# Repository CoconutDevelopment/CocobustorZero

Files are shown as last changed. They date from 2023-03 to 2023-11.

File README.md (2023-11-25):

# CocobustorZero
Voron0

An small upgrade for the Voron 0.2 to make it print slightly faster
BASED ON VORONDESIGN V0.1 https://github.com/VoronDesign/Voron-0
Inspired by 247/0 Beta2

(FORMBOT Full kit possibly comming your way soon)
Join my discord if you want : https://discord.gg/AjryAUX7Z3

Design goals:
- Speedbenchy WR (Sub 2-minute)
  - 1000mm/s Velocity
  - 300000mm/s^2 Acceleration

- 4 motor NEMA17 4WD
  - 48-60mm NEMA17 support
  - Separate control board

- Triple Belted z (worm gearing)
  - Fast Z hops and no z binding
  - Auto bed tramming
  - Ultralow Profile

- External cooling
  - Coconut's Triple Fan Ducts
  - 12KPA CPAP fan

- Extremely Lightweight X gantry
  - Cnc X carriage
  - Bowden Ultralight Toolhead
  - External esp
  - Ultralight Xy joints
  - CNC hollowed mgn7 rail

- Nema17 4WD Coconut edition
  - Extreme motor grip (200+ degrees)
  - Straight belt path
  - Integrated motor idlers
  - Fits all in the back

- Enclosure
    - Has to be enclosable using the 0.2 Tophat
    - Has to be ABS capable
    - All part cooling must draw enclosure air

- M4 Max
    - Strongest extruder possible
    - Double Shear
    - Short Bowden tube

Upgrades:
- 247/0 Beta2 (By 247printing https://247printing.gumroad.com/) (Inspiration)
- AWD NEMA17 V0 CE (V2 Is reccomended) (By Coconut)
- AWD NEMA17 V0 LE (By LittleTimTim https://github.com/LittleTimTim/V0-AWD-Tim-Style)
- Dual Lrs-150s (By Coconut)
- Vzbot inspired frame braces (By Kl3pt https://www.printables.com/model/450049-voron-v0-frame-brace)
- Skr mini e3 v2 + Annex Constellation supernova
- 48V Meanwell UHP-500-48
- Ultralightweight X gantry + XY joints
- Modded Thick Belted Z (By MathmaticalPotato https://github.com/VoronDesign/VoronUsers/tree/master/printer_mods/MathematicalPotato/v0.1_belted_z_drive)
- Coconut triple fan ducts (By Coconut)

Coconut's V0 AWD V2 mod
(On RC1)

https://github.com/CoconutDevelopment/CocobustorZero/assets/110824572/ccff1a14-459e-45de-a45c-08869c3bc4b1

LittleTimTim's V0 AWD mod https://github.com/LittleTimTim/V0-AWD-Tim-Style

https://github.com/CoconutDevelopment/Stock-Voron-0/assets/110824572/6bcad486-bbd0-41eb-bcec-efc06d3bc0a4

Gallery:
Voron0Back

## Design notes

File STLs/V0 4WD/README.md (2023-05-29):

How to choose a awd

Awd TE (Tim edition) and Awd CE (Coconut edition) are very similar in their design, they both have top and bottom motor plates and tensioners.
The difference between them is coconut awd keeps the belt path straight and uses the motors themselves to tension (using an m5 screw) but it uses 4 more idlers (8 more bearings) than tim edition, and is optimized for maximum grip on the motor pulley. While Tim edition uses the middle idler to tension the belts and may not have as much grip.

Please make an imformed descision and this is biased as it is written by coconut, timtim has allowed me to use his files on this repo but you can also visit his own.
Also note that the text above is in referenace to AWD v2 CE, awd v1 does not have tensioners and is no longer maintained.

If you have questions please ask me on the voron discord in the v0 user mods channel (Coconut #1567) Thank you!

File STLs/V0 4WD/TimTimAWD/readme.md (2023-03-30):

# V0-AWD-Tim-Style
Quad motor v0 XY with tensioner

This design was inspired by Coconut & FailFast

Materials needed:

-random filament (I used CF PETG, ABS will do fine) 

-1 printed Top

-1 printed Bottom

-2 printed Uspacers

-28 F623ZZ Flanged Ball Bearing 3x10x4mm (If you print the stock 9mm spacers you don't need as many)

-28 3x5x0.5 mm Shim Spacer Washers

-23 M3x35 Bolts

-8 M3x8-10-12 (I don't remember what exactly I used but one of those)

-4 GT2 20t pulleys 5mm bore

-4 nema 17 steppers of your choice

-4 heatset inserts

-stock y endstop switch & screws

-5 mm GT2 belt width 6mm

-control board that supports at least 6 stepper drivers (I'm using a btt octopus)

Assembly:

Just put it together, if you're building this I trust you.

Tensioning:

When initially installing belts you can leave the slotted center idler loose, 
once belt is installed you can push idler from the build volume side until tensioned
as desired and tighen.

Klipper config:

you'll need to add a stepper_x1 and stepper_y1 with proper pinout and coresponding driver section,
I'll provide my current config in this folder





https://user-images.githubusercontent.com/129321661/228639436-86d11ff1-20ca-46b5-aa57-27f5ffe6771b.mp4

https://user-images.githubusercontent.com/129321661/228639209-f505d235-a20b-4d33-a5d6-68dab8504cda.mp4

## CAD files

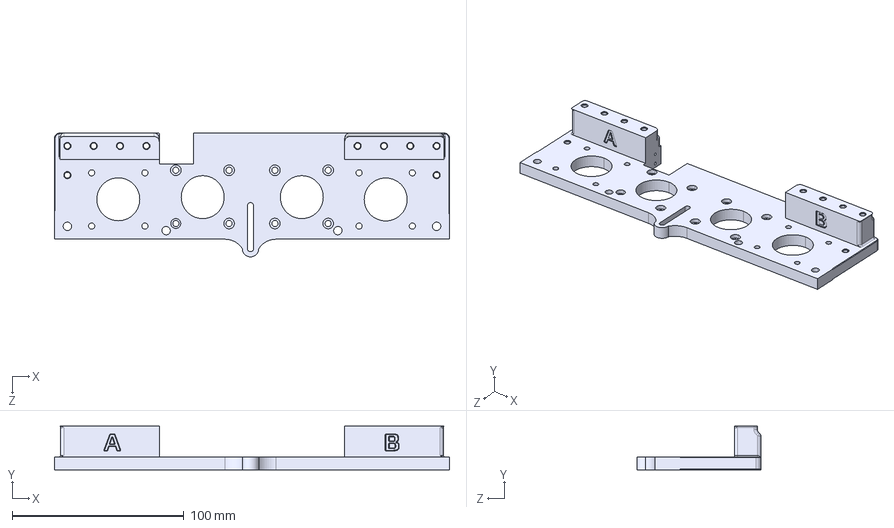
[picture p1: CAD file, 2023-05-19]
STLs/V0 4WD/TimTimAWD/STEP/bottomTotalAssembly.STEP
230.0 x 25.5 x 72.1 mm

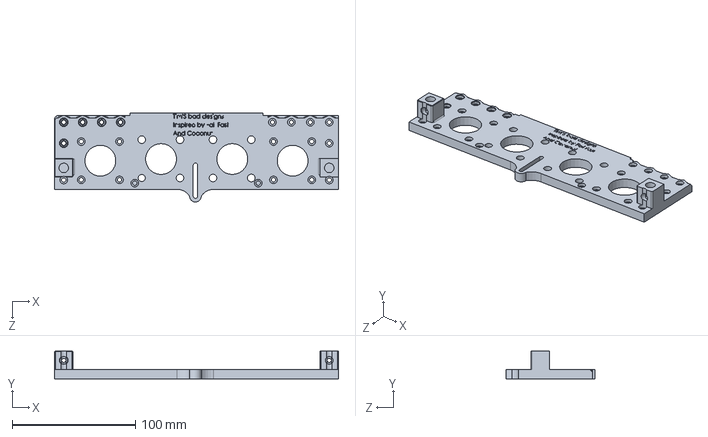
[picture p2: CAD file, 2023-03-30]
STLs/V0 4WD/TimTimAWD/SLDPRTs/TopTotalAssembly.SLDPRT
230.0 x 22.5 x 72.1 mm

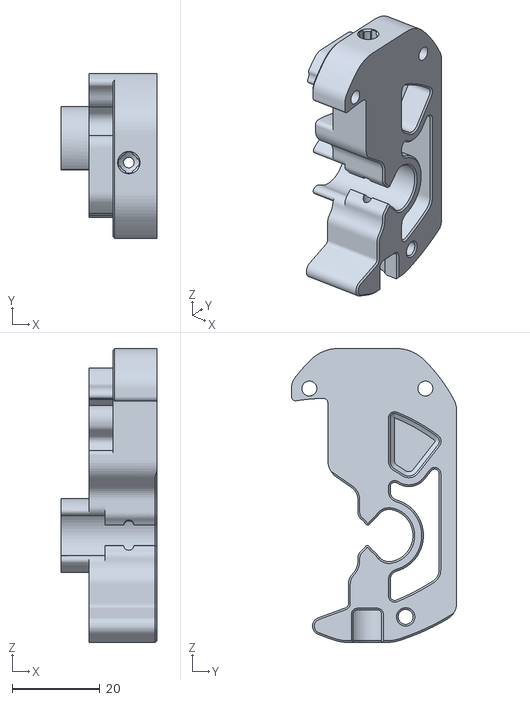
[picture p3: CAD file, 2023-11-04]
STLs/M4max/Main_Body_x1.stl
21.8 x 37.6 x 66.8

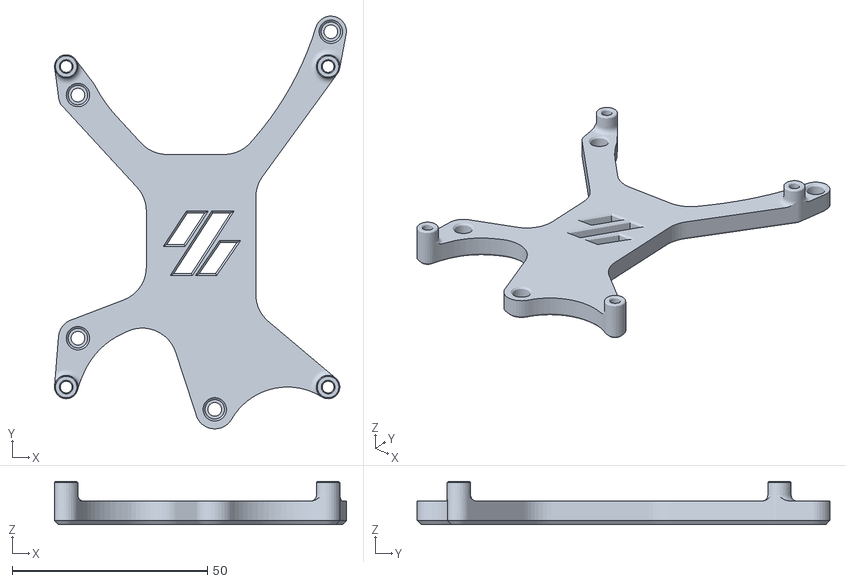
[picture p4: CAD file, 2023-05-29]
STLs/AnnexSupernova/Annex_Supernova_Bracket_Skr_Holes_x1.stl
74.7 x 105.6 x 11.0

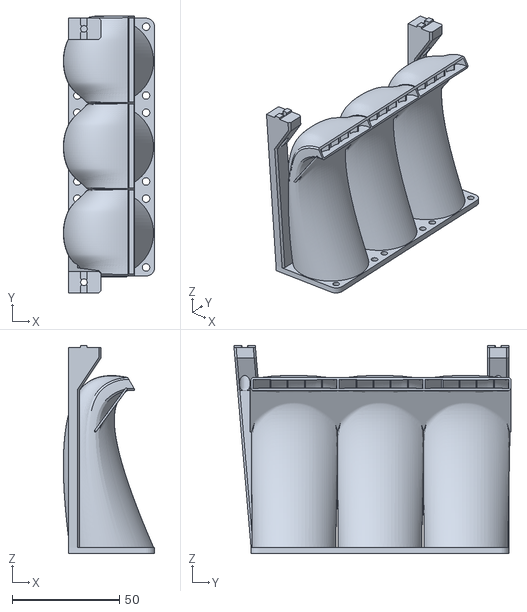
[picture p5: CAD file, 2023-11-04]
STLs/Coconut Air Ducts/[a]_Left_Duct_x1.stl
42.5 x 128.9 x 97.0

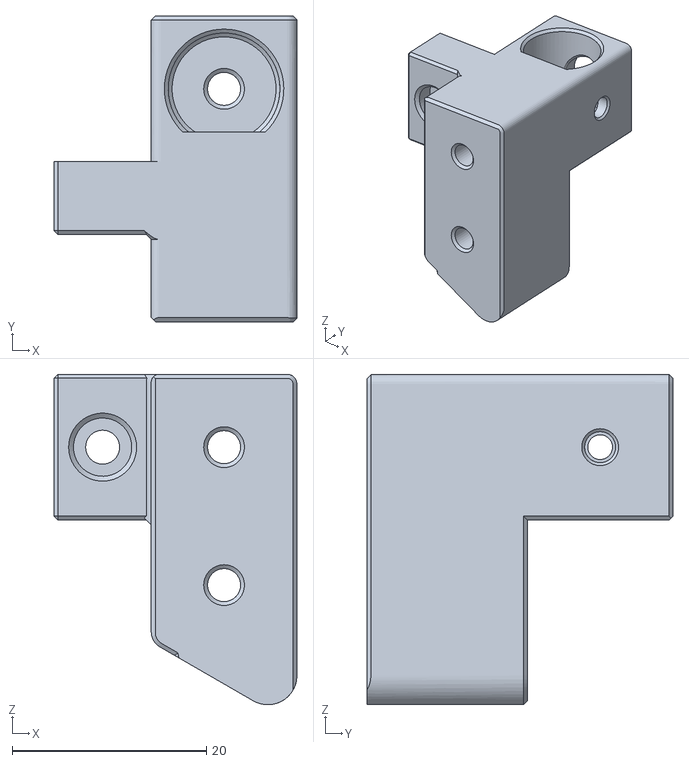
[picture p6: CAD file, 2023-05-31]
STLs/FrontXBeam/A_Upper_Idler_x1.stl
25.0 x 31.5 x 34.0

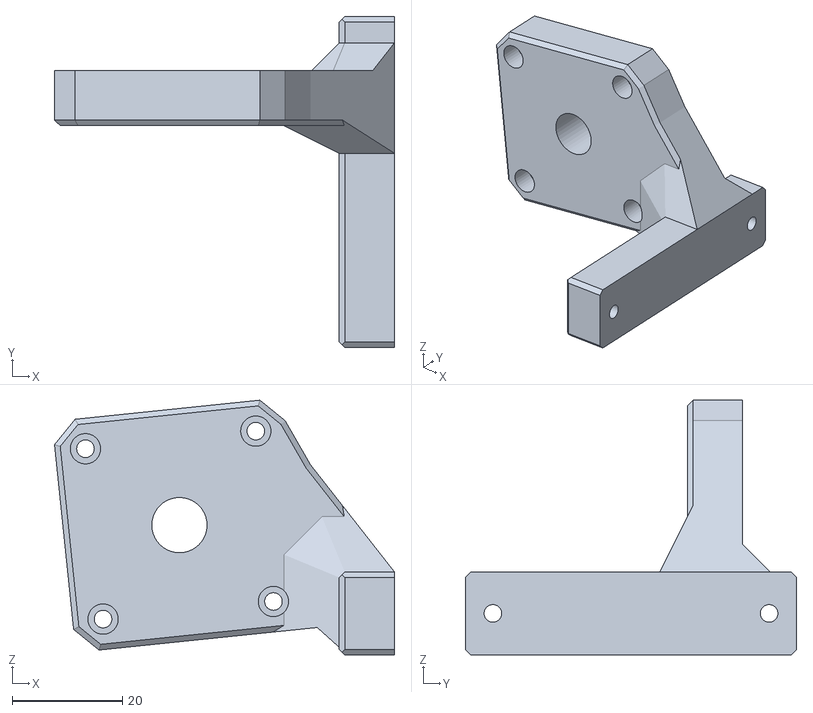
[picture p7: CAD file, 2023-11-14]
STLs/M4max/M4_Max_Motor_Support_x1.stl
61.5 x 60.0 x 46.1

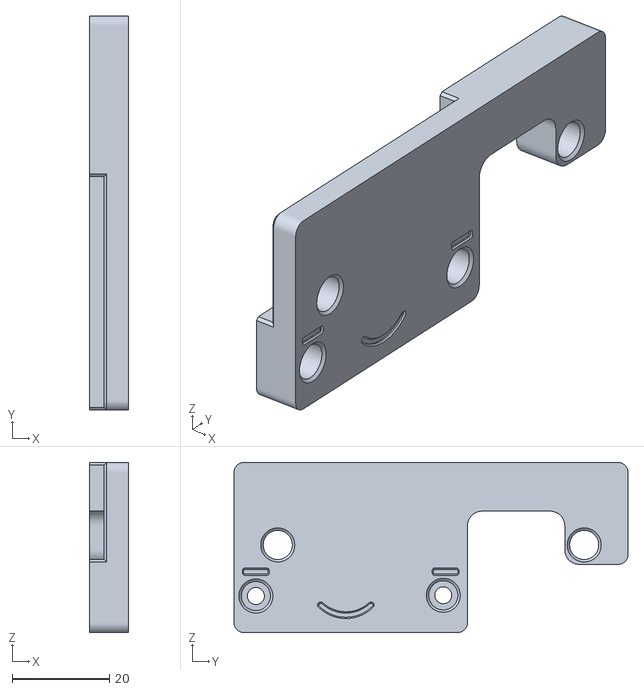
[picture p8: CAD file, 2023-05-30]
STLs/Meanwell UHP-500/[a]_Meanwell_UHP-500_Mount_Lower_x1.stl
8.00 x 81.0 x 35.0

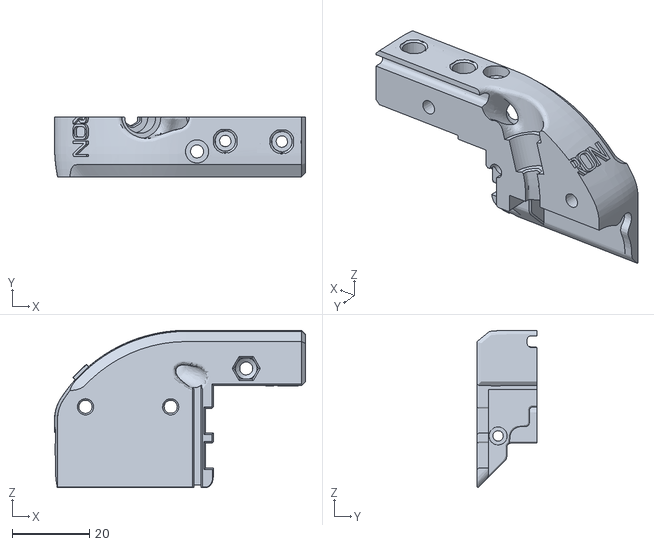
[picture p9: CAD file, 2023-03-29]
STLs/MGN9C X Mosq (Not reccomended)/MGN9CRight.stl
64.8 x 15.4 x 40.6

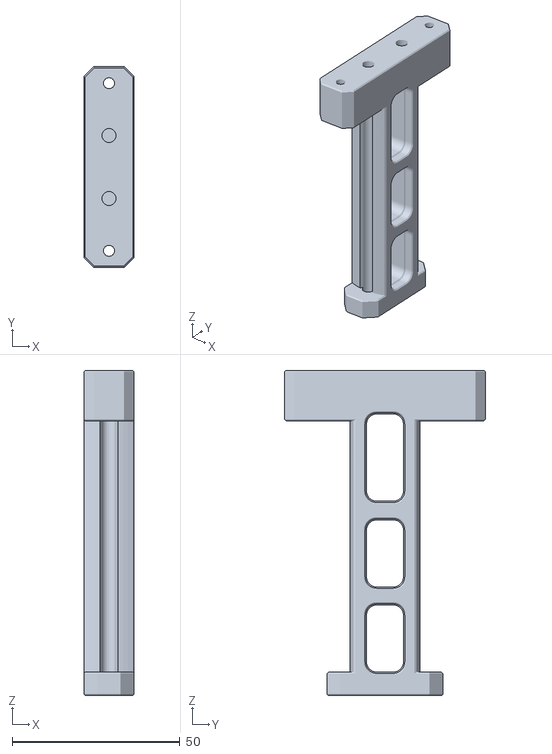
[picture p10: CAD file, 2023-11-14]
STLs/PanelAttachments/Extended_Spool_Holder_x1.stl
15.0 x 60.0 x 97.0

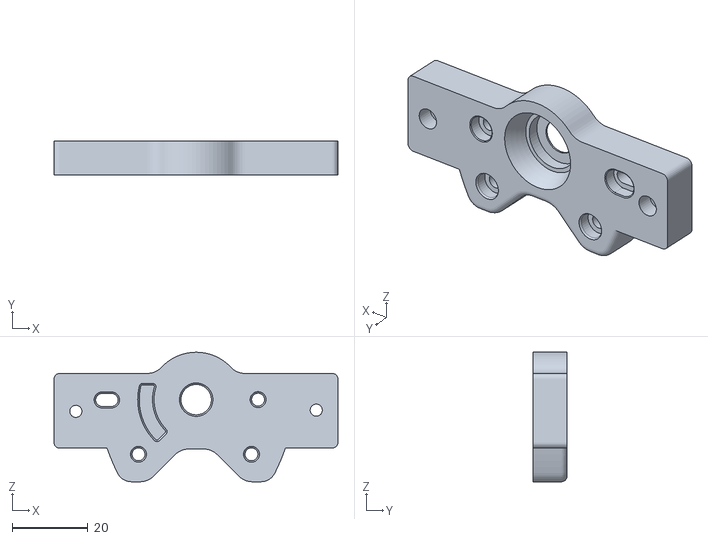
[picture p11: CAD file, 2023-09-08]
STLs/Thick Belted z/Belted_Z_Midplate_x1.stl
74.8 x 9.00 x 34.1

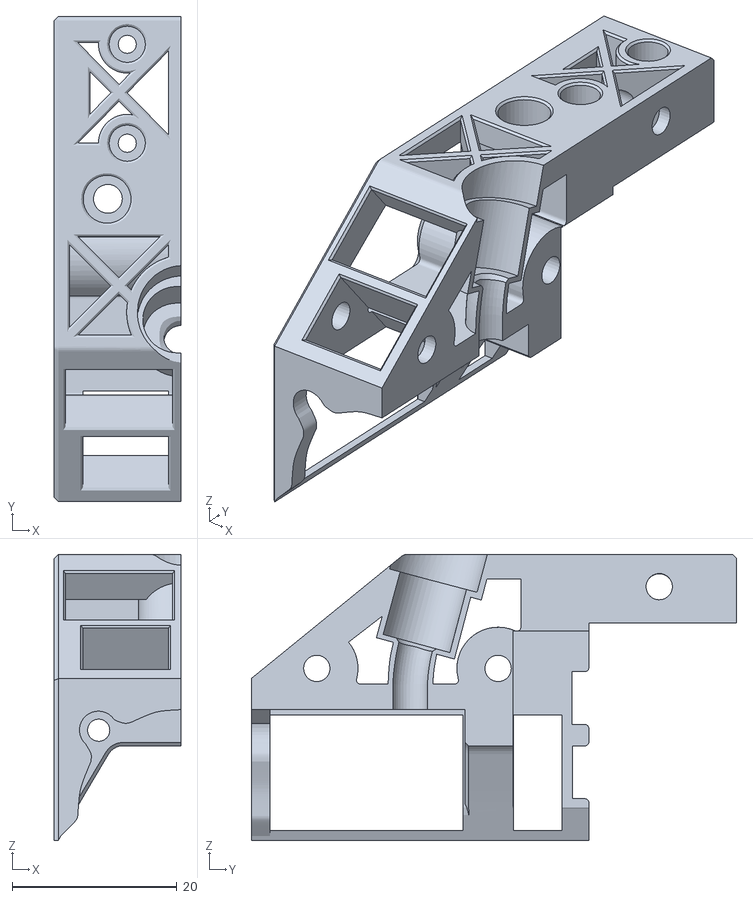
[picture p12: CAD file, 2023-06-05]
STLs/ULW X Gantry/Toolhead/Ultralightweight_Carriage_Left_x1.stl
15.4 x 58.9 x 34.7

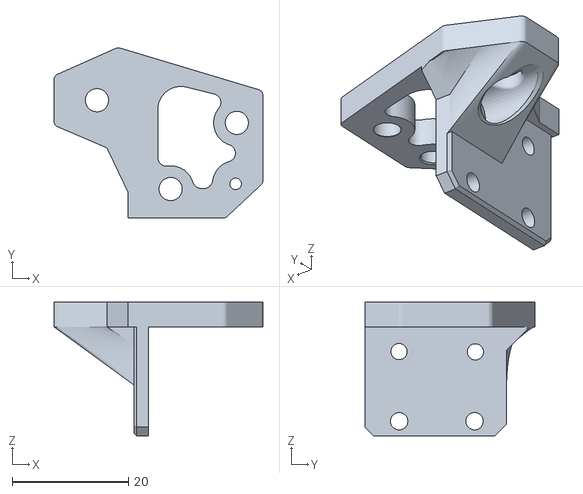
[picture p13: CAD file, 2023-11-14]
STLs/ULW X Gantry/XY Joints/XY_Joint_Right_Lower_x1.stl
36.0 x 29.4 x 23.0

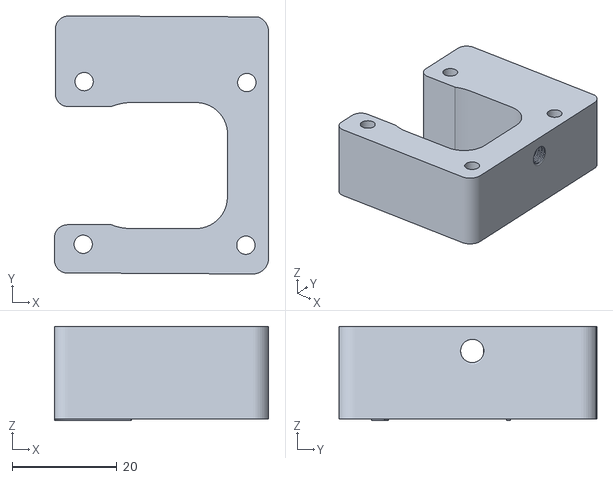
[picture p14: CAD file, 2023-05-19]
STLs/V0 4WD/CoconutAWD/v2AWD (Latest)/[a]_AMotorSpacer_x1.stl
40.8 x 49.2 x 18.0

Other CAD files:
STLs/V0 4WD/TimTimAWD/SLDPRTs/CompleteAWD.SLDASM
STLs/FrontXBeam/B_Upper_Idler_x1.stl
STLs/M4max/End_Plate_x1.stl
STLs/Meanwell UHP-500/[a]_Meanwell_UHP-500_Mount_Upper_x1.stl
STLs/Archived/MGN9C X Mosq/MGN9CLeft_x1.stl
STLs/Archived/V1AWD (OLD)/ABDriveMotorPlate.stl
STLs/Archived/V1AWD (OLD)/ADriveCap.stl
STLs/Archived/V1AWD (OLD)/BDriveCap.stl
STLs/Archived/V1AWD (OLD)/MotorSpacerA.stl
STLs/Archived/V1AWD (OLD)/MotorSpacerB.stl
STLs/M4max/Bottom_Plate_x1.stl
STLs/M4max/Middle_Plate_x1.stl
STLs/M4max/[a]_Guider_x1.stl
STLs/M4max/[a]_Latch_Shuttle.stl
STLs/M4max/[a]_Latch_x1.stl
STLs/MGN9C X Mosq (Not reccomended)/MGN9CLeft.stl
STLs/Superwide Stance/Unfinished (2).stl
STLs/Superwide Stance/Unfinished (3).stl
STLs/Superwide Stance/Unfinished (4).stl
STLs/Superwide Stance/Unfinished.stl
STLs/Thick Belted z/Belted_Z_Back_Plate_x1.stl
STLs/Thick Belted z/Belted_Z_Baseplate_x1.stl
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

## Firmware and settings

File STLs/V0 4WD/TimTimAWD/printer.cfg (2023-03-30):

[include fluidd.cfg]
# This file contains common pin mappings for the BIGTREETECH SKR mini
# E3 v3.0. To use this config, the firmware should be compiled for the
# STM32G0B1 with a "8KiB bootloader" and USB communication.

# The "make flash" command does not work on the SKR mini E3. Instead,
# after running "make", copy the generated "out/klipper.bin" file to a
# file named "firmware.bin" on an SD card and then restart the SKR
# mini E3 with that SD card.

## Voron Design VORON 0.2 SKR Mini E3 V3 config

## *** THINGS TO CHANGE/CHECK: ***
## MCU path                                                                     [mcu] section
## Z and Extruder motor currents                                                [tmc2209 stepper_*] sections. Uncomment the stepper motor you have
## Full steps per rotation for Extruder                                         [extruder] section
## Thermistor types                                                             [extruder] and [heater_bed] sections - See https://www.klipper3d.org/Config_Reference.html#common-thermistors for common thermistor types
## Extruder motor currents                                                      [extruder] section
## PID tune                                                                     [extruder] and [heater_bed] sections
## Fine tune E steps                                                            [extruder] section
## For more info                                                                check https://docs.vorondesign.com/build/startup/#v0

[mcu]
#####################################################################
# Obtain definition by "ls -l /dev/serial/by-id/"
#####################################################################
serial:/dev/serial/by-id/usb-Klipper_stm32f446xx_280022001750344D30353320-if00

[temperature_sensor mcu_temp]
sensor_type: temperature_mcu
min_temp: 0
max_temp: 100

[temperature_sensor host_temp]
sensor_type: temperature_host
min_temp: 10
max_temp: 100

[printer]
kinematics: corexy
max_velocity: 1200
max_accel: 50000
max_z_velocity: 300
max_z_accel: 200
square_corner_velocity: 50

#####################################################################
#   Fan Control
#####################################################################

[heater_fan hotend_fan]
# FAN1
pin: PD13
max_power: 1.0
kick_start_time: 0.5
heater: extruder
heater_temp: 50.0
#fan_speed: 1.0                                                     # You can't PWM the delta fan unless using blue wire

[fan]
# FAN0
pin: PD12
max_power: 1.0
kick_start_time: 0.5                                                # Depending on your fan, you may need to increase this value if your fan will not start
off_below: 0.13
cycle_time: 0.010


#####################################################################
#   Homing and Gantry Adjustment Routines
#####################################################################


[safe_z_home]
home_xy_position: 60,60 										# these coordinates must NOT be greater than the values specified in "position_max:" for the X and Y steppers
speed: 50.0
z_hop: 5

## To be used with BED_SCREWS_ADJUST
[bed_screws]
screw1: 60,5
screw1_name: front screw
screw2: 5,115
screw2_name: back left
screw3: 115,115
screw3_name: back right


#####################################################################
#   V0 Display
#####################################################################
# [mcu display]
# serial: **PASTE YOUR SERIAL PORT HERE AND UNCOMMENT**
# restart_method: command

# [display]
# lcd_type: sh1106
# i2c_mcu: display
# i2c_bus: i2c1a
# # Set the direction of the encoder wheel
# #   Standard: Right (clockwise) scrolls down or increases values. Left (counter-clockwise scrolls up or decreases values.
# encoder_pins: ^display:PA3, ^display:PA4
# #   Reversed: Right (clockwise) scrolls up or decreases values. Left (counter-clockwise scrolls down or increases values.
# #encoder_pins: ^display:PA4, ^display:PA3
# click_pin: ^!display:PA1
# kill_pin: ^!display:PA5
# #x_offset: 2
# #   Use X offset to shift the display towards the right. Value can be 0 to 3
# #vcomh: 0
# #   Set the Vcomh value on SSD1306/SH1106 displays. This value is
# #   associated with a "smearing" effect on some OLED displays. The
# #   value may range from 0 to 63. Default is 0.
# #   Adjust this value if you get some vertical stripes on your display. (31 seems to be a good value)

# [neopixel displayStatus]
# pin: display:PA0
# chain_count: 1
# color_order: GRB
# initial_RED: 0.2
# initial_GREEN: 0.05
# initial_BLUE: 0

# This file contains common pin mappings for the BigTreeTech Octopus
# and Octopus Pro boards. To use this config, start by identifying the
# micro-controller on the board - it may be an STM32F446, STM32F429,
# or an STM32H723.  Select the appropriate micro-controller in "make
# menuconfig" and select "Enable low-level configuration options". For
# STM32F446 boards the firmware should be compiled with a "32KiB
# bootloader" and a "12MHz crystal" clock reference. For STM32F429
# boards use a "32KiB bootloader" and an "8MHz crystal". For STM32H723
# boards use a "128KiB bootloader" and a "25Mhz crystal".

# See docs/Config_Reference.md for a description of parameters.

# Driver0
[stepper_x]
step_pin: PF13
dir_pin: PF12
enable_pin: !PF14
microsteps: 16
rotation_distance: 40
endstop_pin: PG11
position_endstop: 10
position_max: 110
homing_speed: 50

# Driver1
[stepper_y]
step_pin: PG0
dir_pin: PG1
enable_pin: !PF15
microsteps: 16
rotation_distance: 40
endstop_pin: PG10
position_endstop: 0
position_max: 120
homing_speed: 50

# Driver2
#[stepper_z]
#step_pin: PF11
#dir_pin: PG3
#enable_pin: !PG5
#microsteps: 16
#rotation_distance: 8
#endstop_pin: PG10
#position_endstop: 0.5
#position_max: 200

# Driver3
# The Octopus only has 4 heater outputs which leaves an extra stepper
# This can be used for a second Z stepper, dual_carriage, extruder co-stepper,
# or other accesory such as an MMU
#[stepper_]
#step_pin: PG4
#dir_pin: PC1
#enable_pin: PA0
#endstop_pin: PG11
#...

#Driver4
[stepper_x1]
step_pin: PF9
dir_pin: PF10
enable_pin: !PG2
microsteps: 16
rotation_distance: 40
#endstop_pin:  PG11 # T0
#position_endstop: 10
#position_max: 110
#homing_speed: 50

#[filament_switch_sensor material_0]
#switch_pin: PG12

 #Driver5
[stepper_y1]
step_pin: PC13
dir_pin: PF0
enable_pin: !PF1
microsteps: 16
rotation_distance: 40
#endstop_pin: PG10 # T1
#position_endstop: 0
#position_max: 120
#homing_speed: 50

#[filament_switch_sensor material_1]
#switch_pin: PG13

# Driver6
[extruder]
step_pin: PE2
dir_pin: PE3
enable_pin: !PD4
heater_pin: PA2 # HE2
rotation_distance: 40
microsteps: 16
sensor_pin: PF7 # T2
nozzle_diameter: 0.400
filament_diameter: 1.750
sensor_type: Generic 3950
control: pid
pid_Kp: 28.182
pid_Ki: 1.978
pid_Kd: 100.397
min_temp: 0
max_temp: 300
pressure_advance: 1                                               # See tuning pressure advance doc
pressure_advance_smooth_time: 0.080

#[filament_switch_sensor material_2]
#switch_pin: PG14

# Driver7
[stepper_z]
step_pin: PE6
dir_pin: !PA14
enable_pin: !PE0
microsteps: 16
rotation_distance: 8
endstop_pin: PG9 # T3
position_endstop: 0.5
position_max: 120

#[filament_switch_sensor material_3]
#switch_pin: PG15

[heater_bed]
heater_pin: PA1
sensor_pin: PF6 # TB
smooth_time: 3.0
sensor_type: Generic 3950
min_temp: 0
max_temp: 130
control: pid
pid_kp: 68.453
pid_ki: 2.749
pid_kd: 426.122
#[fan]
#pin: PA8

#[heater_fan fan1]
#pin: PE5

#[heater_fan fan2]
#pin: PD12

#[heater_fan fan3]
#pin: PD13

#[heater_fan fan4]
#pin: PD14

#[controller_fan fan5]
#pin: PD15

# CAN bus is also available on this board

########################################
# TMC2209 configuration
########################################

[tmc2209 stepper_x]
uart_pin: PC4
##diag_pin: PG6
run_current: 1
hold_current: 1
stealthchop_threshold: 0

[tmc2209 stepper_y]
uart_pin: PD11
##diag_pin: PG9
run_current: 1
hold_current: 1
stealthchop_threshold: 0

#[tmc2209 stepper_z]
#uart_pin: PC6
##diag_pin: PG10
#run_current: 0.650
#stealthchop_threshold: 0

#[tmc2209 stepper_]
#uart_pin: PC7
##diag_pin: PG11
#run_current: 0.650
#stealthchop_threshold: 0

[tmc2209 stepper_x1]
uart_pin: PF2
run_current: 1
hold_current: 1
stealthchop_threshold: 0

[tmc2209 stepper_y1]
uart_pin: PE4
run_current: 1
hold_current: 1
stealthchop_threshold: 0

[tmc2209 extruder]
uart_pin: PE1
run_current: 0.800
hold_current: .8
stealthchop_threshold: 0

[tmc2209 stepper_z]
uart_pin: PD3
run_current: .8
hold_current: .8
stealthchop_threshold: 0

########################################
# TMC2130 configuration
########################################

#[tmc2130 stepper_x]
#cs_pin: PC4
#spi_bus: spi1
##diag1_pin: PG6
#run_current: 0.800
#stealthchop_threshold: 999999

#[tmc2130 stepper_y]
#cs_pin: PD11
#spi_bus: spi1
##diag1_pin: PG9
#run_current: 0.800
#stealthchop_threshold: 999999
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

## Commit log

2023-03-29 Init Commit
    [ABDriveMotorPlate.stl, ADriveCap.stl, BDriveCap.stl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]
2023-03-29 Init commit
    Adding nut carrier later
    [MGN9CLeft.stl, MGN9CRight.stl]
2023-03-30 Tim Files
    https://github.com/LittleTimTim/V0-AWD-Tim-Style
    [CompleteAWD.SLDASM, TopTotalAssembly.3MF, TopTotalAssembly.SLDPRT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]
2023-05-17 Upload v2 files
    V2 has a all new belt tensioner system and improved rigidity
    [BottomMotorPlate_x1.stl, TopMotorPlatex1.stl, [a]_AB1_Spacer_x2.stl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]
2023-05-17 Add Awd v2 files
    [BottomMotorPlate_x1.stl, TopMotorPlatex1.stl, [a]_AB1_Spacer_x2.stl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]
2023-05-18 v2 fix
    [BottomMotorPlate_x1.stl]
2023-05-19 Added V2 cad file
    [TopMotorPlate_x1.stl, TopMotorPlatex1.stl]
2023-05-28 Added ultralightweight X joints and Uhp-500 mount
    [MGN9CLeft.stl, MGN9CRight.stl, Meanwell_UHP-500_Mount_Lower_x1.stl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]
2023-05-29 New xy joints
    [XY_Joint_Left_Lower_x1.stl, XY_Joint_Left_Upper_x1.stl, XY_Joint_Right_Lower_x1.stl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]
2023-05-29 Add master CAD file
2023-05-29 Added new ducts
    [ABDriveMotorPlate.stl, ADriveCap.stl, BDriveCap.stl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]
2023-05-29 Add archived
    [BottomMotorPlate_x1.stl, CompleteAWD.SLDASM, TopMotorPlate_x1.stl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]
2023-05-30 Fix PSU mounting
    [Meanwell_UHP-500_Mount_Lower_x1.stl, [a]_Meanwell_UHP-500_Mount_Lower_x1.stl, [a]_Meanwell_UHP-500_Mount_Upper_x1.stl]
2023-05-31 Added new XY and front X
    [A_Upper_Idler_x1.stl, B_Upper_Idler_x1.stl, XY_Joint_Left_Lower_x1.stl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]
2023-05-31 Forgot to add lower joints lol
    [XY_Joint_Left_Lower_x1.stl, XY_Joint_Left_Upper_x1.stl, XY_Joint_Right_Lower_x1.stl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]
2023-05-31 Fixed XY joint
    [MGN9CLeft_x1.stl, MGN9CRight_x1.stl]
2023-06-03 Added ULW Carriage
    [Ultralightweight_Carriage_Left_x1.stl, Ultralightweight_Carriage_Right_x1.stl, XY_Joint_Left_Lower_x1.stl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]
2023-06-04 Added Fixed LW carriage
    [Ultralightweight_Carriage_Left_Mosq_x1.stl, Ultralightweight_Carriage_Left_x1.stl, Ultralightweight_Carriage_Right_Mosq_x1.stl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]
2023-06-04 Added New ULW carriage
    [Ultralightweight_Carriage_Left_x1.stl, Ultralightweight_Carriage_Right_x1.stl]
2023-06-04 New new new Carriage ultralight
    [Ultralightweight_Carriage_Left_x1.stl, Ultralightweight_Carriage_Right_x1.stl]
2023-06-05 Ultralightweight Carriage V5
    [Ultralightweight_Carriage_Left_x1.stl, Ultralightweight_Carriage_Right_x1.stl]
2023-06-06 Beta Feet
    [Unfinished (2).stl, Unfinished (3).stl, Unfinished (4).stl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]
2023-09-08 Uploaded new fixed xy joints
    [XY_Joint_Left_Upper_x1.stl, XY_Joint_Right_Upper_x1.stl]
2023-09-08 Added BeltedZ
    [Belted_Z_Back_Plate_x1.stl, Belted_Z_Baseplate_x1.stl, Belted_Z_BedMount_x1.stl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]
2023-09-08 Fixed Joints x2 (Thanks to kirapatka)
    [XY_Joint_Left_Upper_x1.stl, XY_Joint_Right_Upper_x1.stl]
2023-11-04 Add new ducts
    3 fans
    [[a]_Left_Duct_x1.stl]
2023-11-04 Add m4 max stls
    [Bottom_Plate_x1.stl, End_Plate_x1.stl, Main_Body_x1.stl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]
2023-11-05 Update m4 files
    [[a]_Latch_Shuttle.stl]
2023-11-14 Reinforce XY joints
    [XY_Joint_Left_Lower_x1.stl, XY_Joint_Left_Upper_x1.stl, XY_Joint_Right_Lower_x1.stl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]
2023-11-14 Revise parts
    [End_Plate_x1.stl, Extended_Spool_Holder_x1.stl, M4_Max_Motor_Support_x1.stl]
